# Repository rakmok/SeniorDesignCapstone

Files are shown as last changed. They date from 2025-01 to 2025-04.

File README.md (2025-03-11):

# SeniorDesignCapstone

This is the repository to record and motivate our capstone project for ECE 445: Senior Design in the Spring of 2025 titled PawFeast: Food on Demand. The group members are Arash Amiri, Kathryn Thompson, and Omkar Kulkarni.

The project entails the analysis, design, and build of a pet food dispensory system. If you wish to see each member's notebook, you can switch branches in github.com by clicking main or run git checkout \[member_first_name]-notebook. Each member hosts their own notebook on a different branch. The Hardware folder contains all of our KiCAD boards and other libraries. The images folder is only meant for displaying images to the README and the Assignments folder includes all of our important documents.

# Problem

All household pet owners must remember to feed their pets—whether they are birds, guinea pigs, rabbits, dogs, or cats—at set periods during the day. But there can be times when people forget to feed their pets, double feed them, or have trouble feeding them on schedule. This can be due to poor communication between family members or even occur when pet owners come home late from work or prior commitments. During these times, pets either overeat, go hungry, or eat irregularly. As a result, timer-based pet feeders have been developed to release food at set intervals. When food sits out for extended periods of time, the risk of the food becoming stale or getting infected with bugs increases drastically.

If an insect is near your food, it is a common reaction to remove or swat it away, but that mechanism is not present for the pet’s food bowl, especially when the family is not at home. Another issue is that smarter pets can nose into the food storage and overeat or eat something that their bodies will reject (like chocolate for dogs). With a set schedule to limit food dispensation throughout the day, the pet will not take advantage of either a careless overpour of food or of an unmanned food station. Furthermore, data on how much food was dispensed and eaten will help track and optimize the pet’s eating habits.

# Solution

We are seeking to solve this problem by having timers coupled with a button and RFID component to release food—thus preventing overeating. Given all of these conditions, the dispenser will release the pet food. This ensures that the pet is not only fed on time, but that the food is not polluted when the pet goes to eat; additionally, a chime will go off signaling to the pet that it is time for them to eat. We will incorporate a notification system to alert the owner(s) whether the pet has eaten or when the food store has low levels of food.

If the pet were to not eat all the food at once and leave the food dispenser, the pressure sensor will tell the dispenser to cover the food until the pet returns ensuring freshness and preventing bugs.

# Solution Components

## Subsystem 1: Refilling Food Store

The subsystem for checking if the food store is empty will include a through-beam optical sensor that is able to determine whether an object is present—this will serve to detect whether the food inside of the container is low and needs to be refilled. When the food store reaches a certain level, a signal will be sent to subsystem 6 (the brain), which will send an automated message to notify the owner to refill the food store.

## Subsystem 2: Power System

The power system will supply energy to all of the various subsystems, including the microcontroller of subsystem 6 (the brain), the stepper motor driver in subsystem 3, and the various sensors in subsystems 1 (refilling food) and 3 (food dispenser). The low voltage buses will be 3.3V, 12V, and 5V, all of which will be powered by a combination of rechargeable lithium-ion batteries with voltage regulators and buck converters. This compact, custom 3s2p battery pack will allow the pet dispenser to be portable, even for family vacations or road trips—more importantly, it will provide a steady current, even when the pack voltage drops (unlike standard AA/AAA cells). The 12V to 3.3V regulator chip will be Monolithic Power Systems’s MP2315SGJ-Z, which can take a 12V input and output up to 2.5A [4.7]. The 12V to 5V regulator chip will be Monolithic Power Systems’s MP2338GTL-Z [4.6]. The 12V input into the motor driver IC circuit will come straight from the battery pack. There will also be a backup supply voltage of 5V from a typical barrel jack wall-outlet, integrated into the brain board. This will implement the AMS1117 LDO, which is perfect for 5V to 3.3V power conversion. Just to be clear, this 5V barrel-jack addition will just be included on the brain board as a backup power subcircuit in case of power shutdown.

## Subsystem 3: Food Dispenser

This subsystem will utilize a E Series Nema 17 stepper motor that will rotate a door to the food container when needed and allow a set amount of food through before rotating again to close the door [4.8]. The motor will be controlled by a stepper motor controller IC (DRV8825) with a custom control circuit that takes in 12V and outputs 3.4V to the motor. We will define hard cut offs that will be coded for maximum amount of food to be dispensed and specify times at which food may be dispensed during the day.

The main objective of this subsystem is to make the system an on-demand food system. We will utilize a large button for the dog to step on when hungry. When pressed, the system will start the motors to release food, on the condition that enough time has elapsed since it ate last. The pet would be trained how to ask for food using this button. Only when the button is pressed and enough time has passed, will food then be dispensed.

## Subsystem 4: RFID for pet identification

We will have a receiver for a minimum of 2 HF RFID tags 9662 Long Distance Passive Alien H3. We will use the RC522 RFID chip for reading and writing to the RFID chips. The RFIDs would be used to signal which pet is using the dispenser, so the owner is able to utilize the same dispenser for one or more pets.

## Subsystem 5: User Interface

The subsystem for notifications will be a web application that we will build that is able to connect with the pet feed dispenser system. For the application side, we will utilize Bottle for our backend, SQLite for our database, and html pages for our frontend to create a user friendly method to check the pet’s eating habits. This will notify users for when the pet has been fed, if the food tank is low and requires refiling, and if the food was covered due to an empty bowl or a partially filled one.

## Subsystem 6: Brain

The brain subsystem will take in inputs from all of the other sensor subsystems and output the according signals to the user interface (for notifications) and the food dispenser motor driver. This system will also track the amount of time that has passed and sound a soft chime for when enough time has passed for the pet to be able to eat. The ESP32 WROOM-32E-4N microcontroller, known for its wifi connectivity and security measures, would have a set of I/O pins for taking in these signals. This MCU programmer circuit and other control level circuitry—firmware or equivalent—would be incorporated onto this board along with a UART circuit to detect pet RFIDs (done with the UHF RFID reader JRD-4035).

# High Level Requirements List

For this project to be considered successful, our project must meet the following requirements:

- The **Pet Food Dispenser** must **not** dispense food before user preset times, such as **10 AM and 6 PM, daily**, with a **10-minute tolerance**.
- The **Pet Food Dispenser** must dispense food into the **designated food bowl** upon detecting the **presence of the pet** via the **button** and the **2+ RFID tags** on the pet’s collar **within 2 minutes**.
- The **user interface** must update **within 5 minutes** of an event on the application we create, detailing:
  - The pet’s **feeding status**
  - **Low food store** notifications at **20% & 10%**
  - **Unfinished meals**

# Results

TBA

# Schematic

TBA

# Figures

TBA

# Demo

TBA

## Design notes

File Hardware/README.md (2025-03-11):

# KiCAD Board Repository

This is the hardware repository with all of our KiCAD boards. We have five: two power boards, a brain board, an RFID board, and the motor driver board. If you are unable to see symbols on the schematic capture, you will need to go to schematic editor->Preferences->Configure Paths and manually add a large parts library that you can link from Hardware/Libraries folder courtesey of Illini Solar Car.

For all of the parts that we dowloaded from 3rd party sites, there is a folder called Parts (Hardware/Parts), which has the symbols, footprints, and some .step files. This can be linked by going to schematic editor->Preferences->Manage Symbol Libraries. The same must be done for all the footprints in the PCB editor under Preferences->Manage Footprint Libraries. Three images below depict the path libraries for Omkar's KiCAD. Note that Omkar's file path for the Solar Car library is completely different and the Parts library is about three steps upstream from what you should link—you should add SeniorDesignCapstone/Hardware/Parts as your filepath instead of ../ECE445/Parts. There is also a courtesey template to get started, though you will need to set up the Illini Solar Car Libraries folder or you won't be able to retrieve parts with the 'a' hotkey.

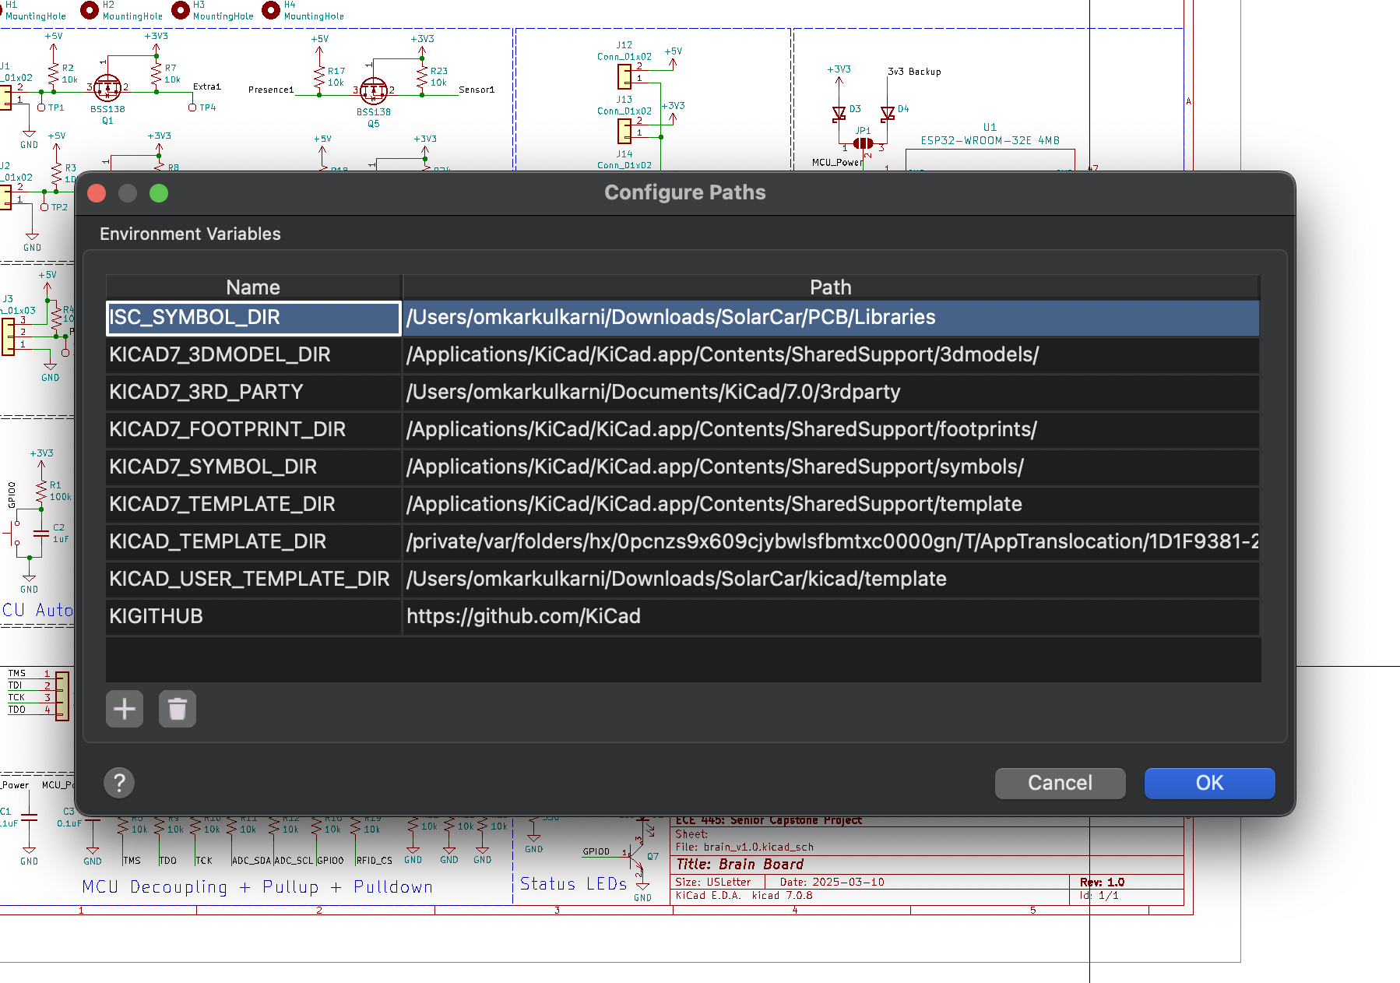
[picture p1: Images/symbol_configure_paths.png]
Configure Path

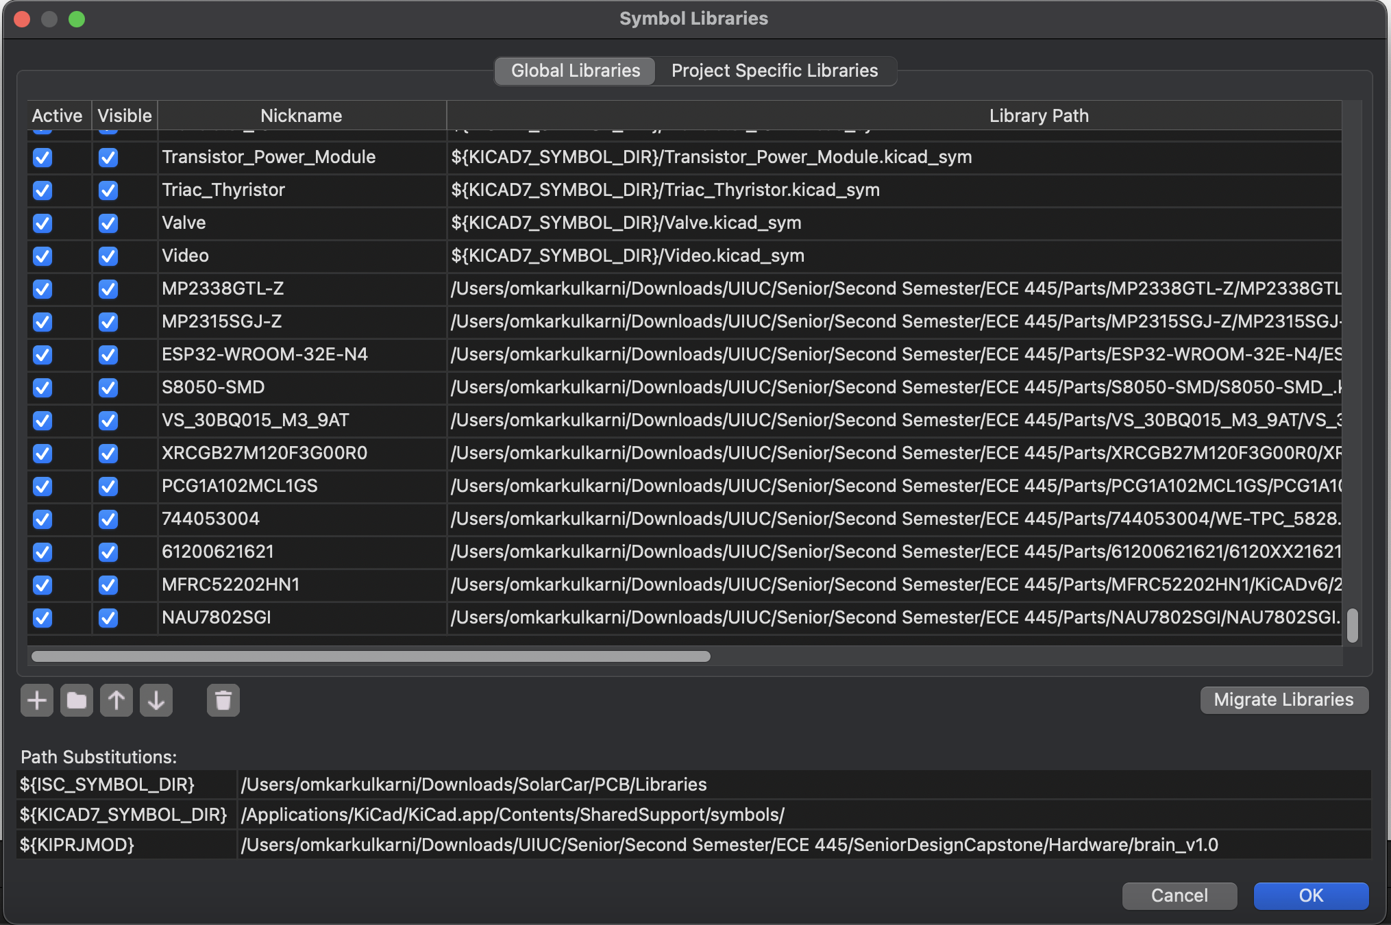
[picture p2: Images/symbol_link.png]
Download and Link Symbols

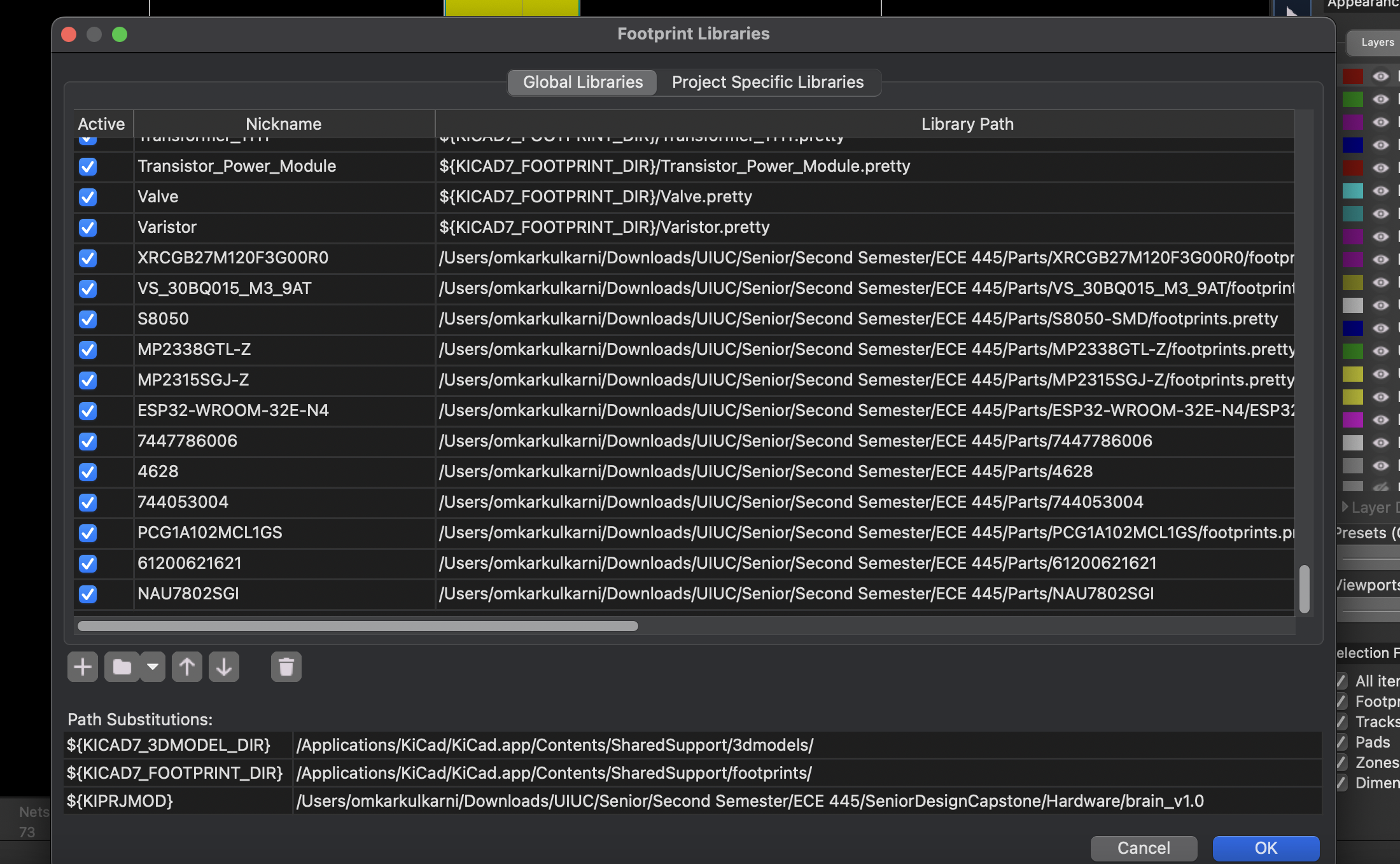
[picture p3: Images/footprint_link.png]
Download and Link Footprints


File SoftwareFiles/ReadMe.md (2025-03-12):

# Software Files for Team 30's Group Project for ECE445 at UIUC

This Markdown file will be used to describe the different files in this folder and what they do. Files that start with Arduino are comptible and tested on the Arduino UNO dev board for the breadboard demo. This code has been developed based on the provided starter code available on the distributer's website. We have included the links below for convenience.        

Works Cited:  
- [RFID](https://www.electronicwings.com/esp32/rfid-rc522-interfacing-with-esp32)
- [Load Cell (LC)](https://learn.adafruit.com/adafruit-nau7802-24-bit-adc-stemma-qt-qwiic/arduino) 
- [Presence Sensor (PS)](https://learn.adafruit.com/ir-breakbeam-sensors/arduino) 

The current organization of this folder is as follows:  
  [SoftwareFiles](./)  
  |-> [Arduino_RFID.cpp](./Arduino_RFID.cpp)  
  |-> [Arduino_LC.cpp](./Arduino_LC.cpp)  
  |-> [Arduino_PS.cpp](./Arduino_PS.cpp)  
  |-> [Arduino_RFID_LC_PS.cpp](./Arduino_RFID_LC_PS.cpp)

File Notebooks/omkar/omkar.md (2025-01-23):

# Omkar's Digital Notebook

This file serves as a digital notebook for my ECE 445: Senior Design project.

# 01/21/2025

After the first ECE 445 lecture, the group assembled to discuss and hash-out viable ideas for our project. We had previously met during winter break and gone through a number of project ideas related to solar power, cybersecurity, microcontroller development, vehicle architecure, cell balancing, and smart charging. In this session, the group researched ideas that fit the complexity and scope of what we believed was expected of us by the course staff. We made an initial project proposal post on the web board on smart charging technology, which includes battery health monitoring, voltage/current control, possibly the abilility to set charging percentage, and the ability to charge laptop-to-laptop. In this process, we discarded ideas related to cell-balancing and security because they were either too complex to implement or the group (as a whole) did not have enough expertise to pursue the idea.

We got an opportunity to ask the head TA about course logistics and project complexity. His feedback suggested that laptop-to-phone charging was too simple and if we wanted to work on high-voltage charging, every member of the group would need to get trained. Currently, we are assessing what is possible to complete within a semester and still complex enough to aim for being a featured project.

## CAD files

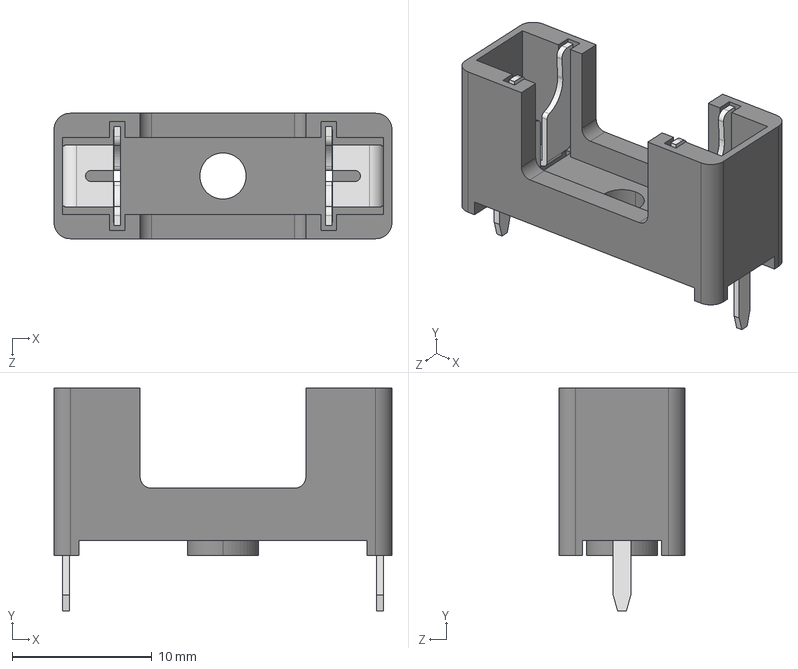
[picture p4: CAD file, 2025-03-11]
Hardware/Parts/4628/4628.step
24.2 x 16.0 x 8.99 mm

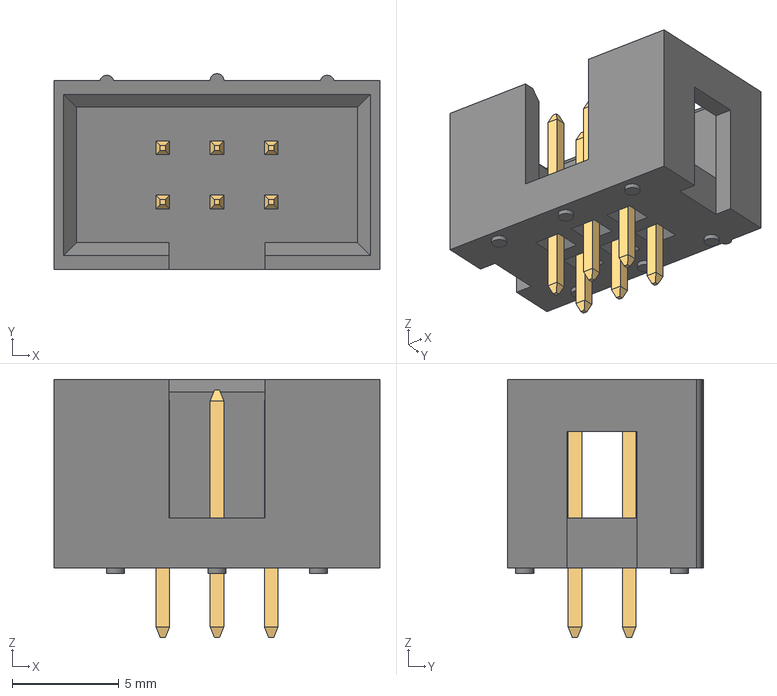
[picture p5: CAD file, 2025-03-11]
Hardware/Parts/61200621621/6120XX21621_61200621621.step
15.3 x 9.18 x 12.1 mm
6120xx21621_PIN x 6

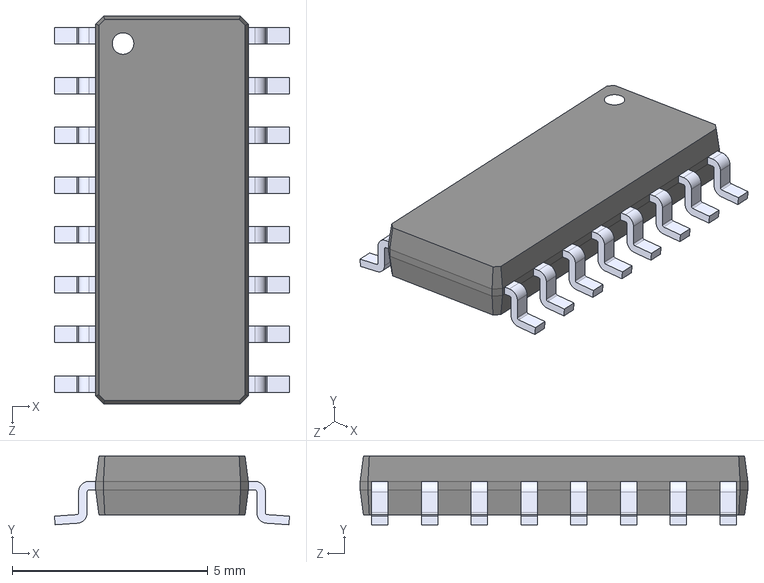
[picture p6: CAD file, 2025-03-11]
Hardware/Parts/NAU7802SGI/NAU7802SGI.step
6.00 x 1.75 x 9.90 mm

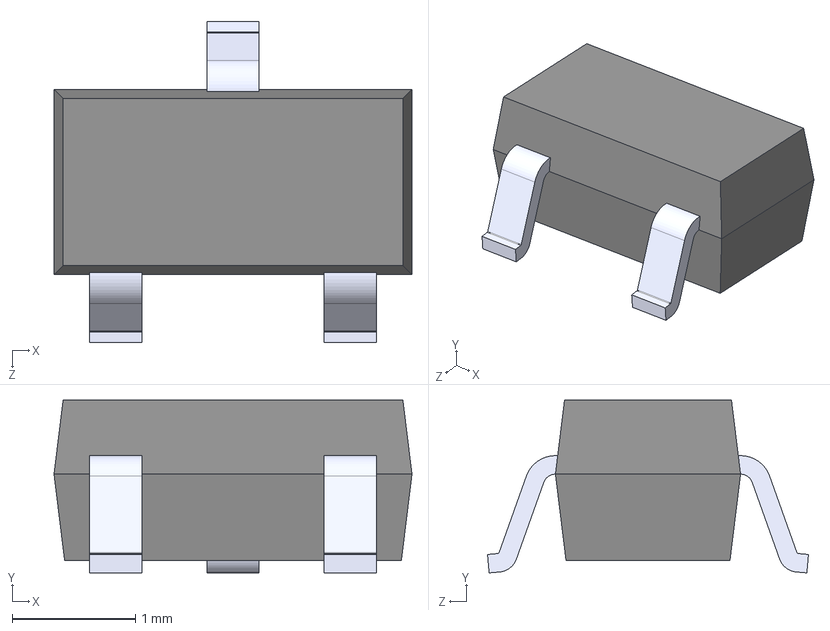
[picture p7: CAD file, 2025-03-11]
Hardware/Parts/S8050-SMD/S8050-SMD.step
2.90 x 1.40 x 2.60 mm

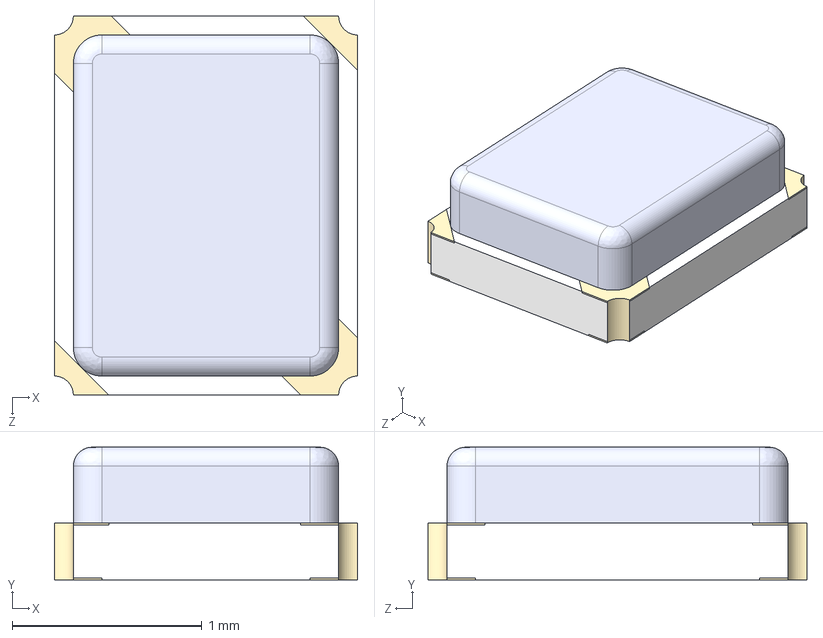
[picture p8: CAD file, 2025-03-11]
Hardware/Parts/XRCGB27M120F3G00R0/XRCGB27M120F3G00R0.step
1.60 x 0.7 x 2.00 mm

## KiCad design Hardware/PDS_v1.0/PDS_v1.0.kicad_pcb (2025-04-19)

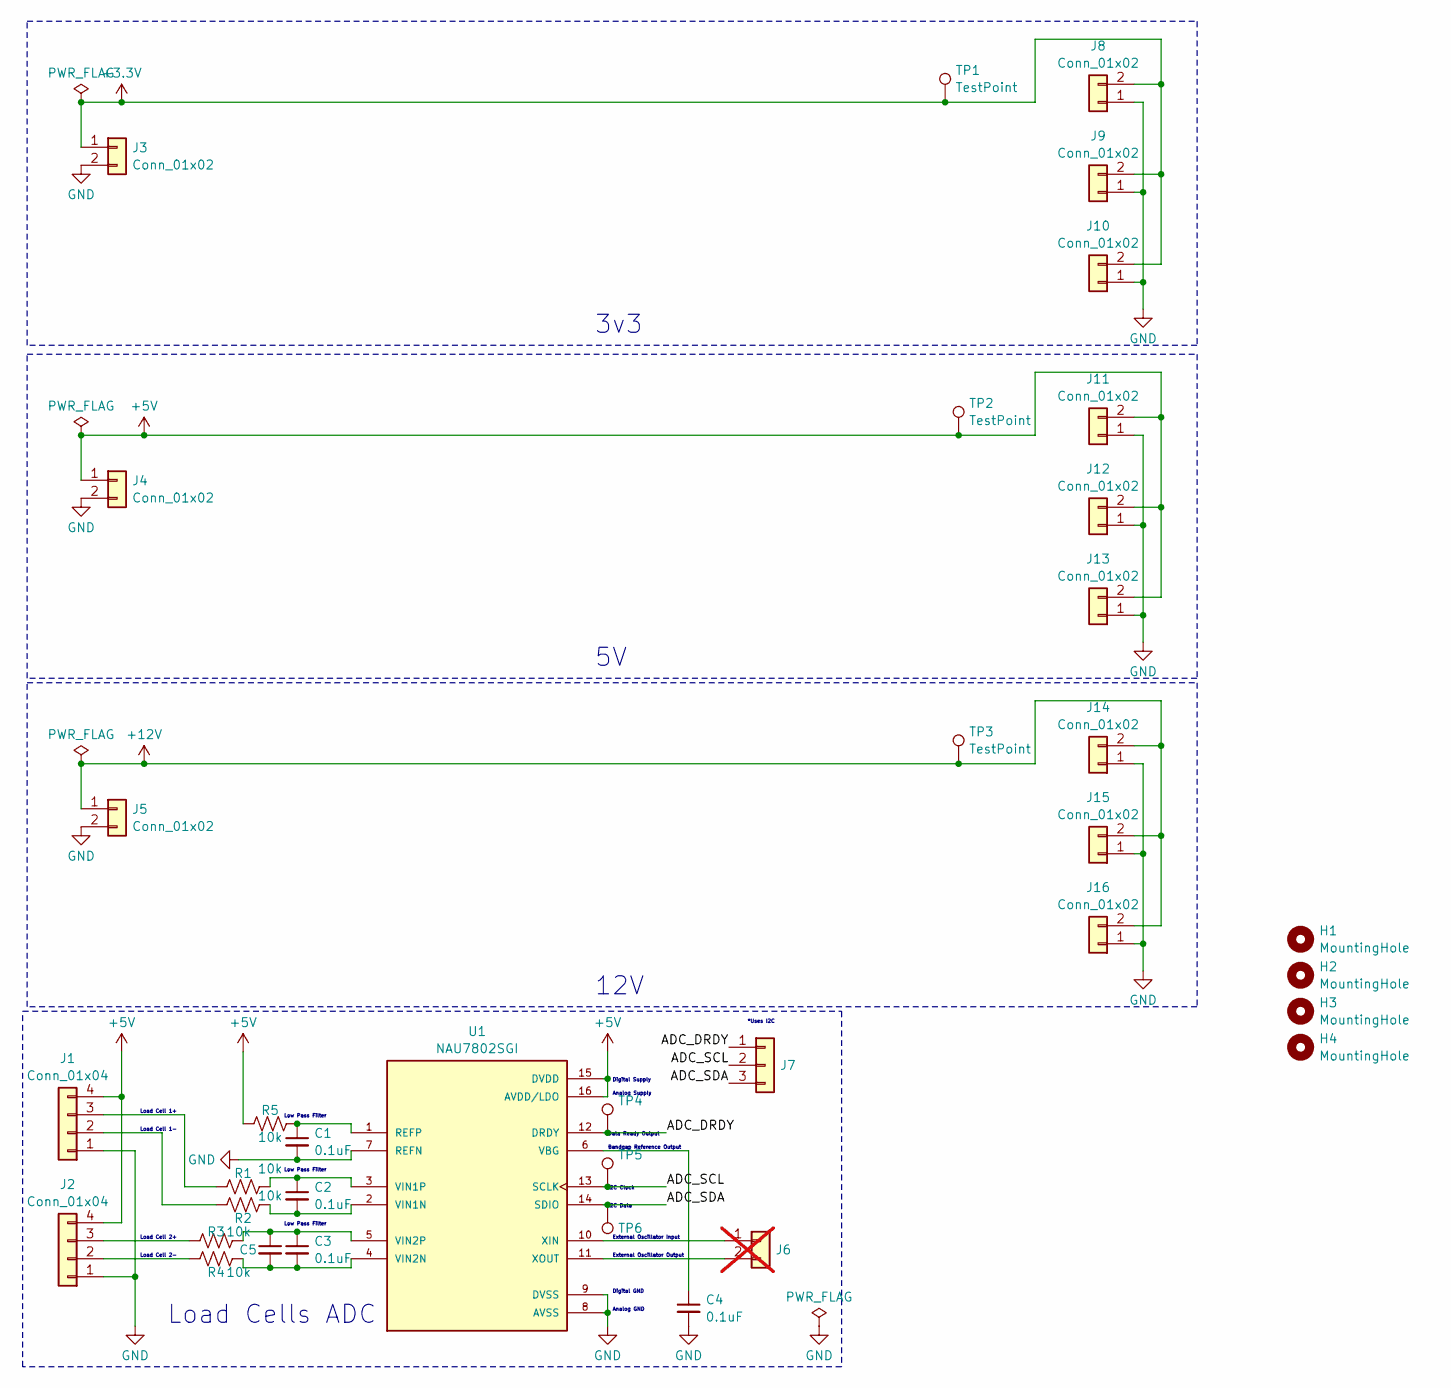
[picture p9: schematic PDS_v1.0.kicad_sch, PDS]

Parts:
C1, C2, C3, C4: 0.1uF; C_0805_2012Metric; MPN CC0603KRX7R7BB104
C5: 470uF; C_Radial_D10.0mm_H12.5mm_P5.00mm
H1, H2, H3, H4: MountingHole; MountingHole_3.2mm_M3; MPN NA
J1, J2: Conn_01x04; Molex_KK-254_AE-6410-04A_1x04_P2.54mm_Vertical; MPN 0022292041
J3, J4, J5, J8, J9, J10, J11, J12, J13, J14, J15, J16: Conn_01x02; Molex_KK-254_AE-6410-02A_1x02_P2.54mm_Vertical
J6: Conn_01x02; Molex_KK-254_AE-6410-02A_1x02_P2.54mm_Vertical; not fitted
J7: Conn_01x03; Molex_KK-254_AE-6410-03A_1x03_P2.54mm_Vertical
R1, R2, R3, R4, R5: 10k; R_0805_2012Metric; MPN HRG3216P-1002-B-T1
TP1, TP2, TP3, TP4, TP5, TP6: TestPoint; TestPoint_Keystone_5010-5014_Multipurpose
U1: NAU7802SGI; SOIC127P600X175-16N; PARTREV 2.6

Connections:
+3V3: J3.1, J8.2, J9.2, J10.2, TP1.1
+5V: J1.4, J2.4, J4.1, J11.2, J12.2, J13.2, R5.1, TP2.1, U1.15 (DVDD), U1.16 (AVDD/LDO)
+12V: J5.1, J14.2, J15.2, J16.2, TP3.1
/ADC_DRDY: J7.1, TP4.1, U1.12 (DRDY)
/ADC_SCL: J7.2, TP5.1, U1.13 (SCLK)
/ADC_SDA: J7.3, TP6.1, U1.14 (SDIO)
GND: C1.2, C4.2, J1.1, J2.1, J3.2, J4.2, J5.2, J8.1, J9.1, J10.1, J11.1, J12.1, J13.1, J14.1, J15.1, J16.1, U1.7 (REFN), U1.8 (AVSS), U1.9 (DVSS)
unnamed: J1.2, R2.1
unnamed: J1.3, R1.1
unnamed: J2.2, R4.1
unnamed: J2.3, R3.1
unnamed: J6.1, U1.10 (XIN)
unnamed: J6.2, U1.11 (XOUT)
unnamed: C1.1, R5.2, U1.1 (REFP)
unnamed: C4.1, U1.6 (VBG)
unnamed: C2.2, R2.2, U1.2 (VIN1N)
unnamed: C2.1, R1.2, U1.3 (VIN1P)
unnamed: C3.2, C5.2, R4.2, U1.4 (VIN2N)
unnamed: C3.1, C5.1, R3.2, U1.5 (VIN2P)

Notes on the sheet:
Load Cell 2-
Low Pass Filter
Analog GND
3v3
Load Cell 2+
Load Cell 1+
12V
Analog Supply
Digital Supply
*Uses I2C
Load Cells ADC
Bandgap Reference Output
External Oscillator Input
Data Ready Output
Digital GND
I2C Data
External Oscillator Output
Load Cell 1-
I2C Clock

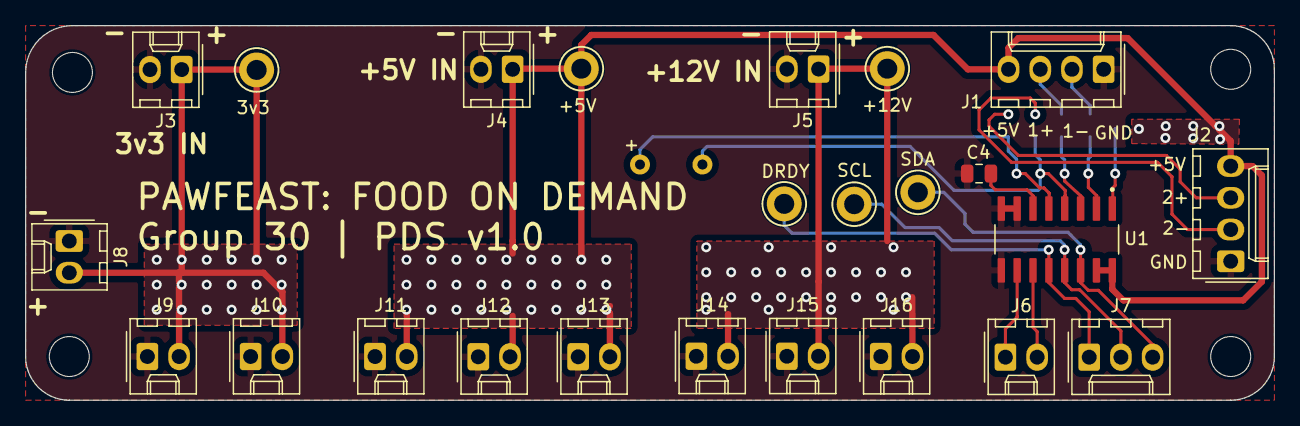
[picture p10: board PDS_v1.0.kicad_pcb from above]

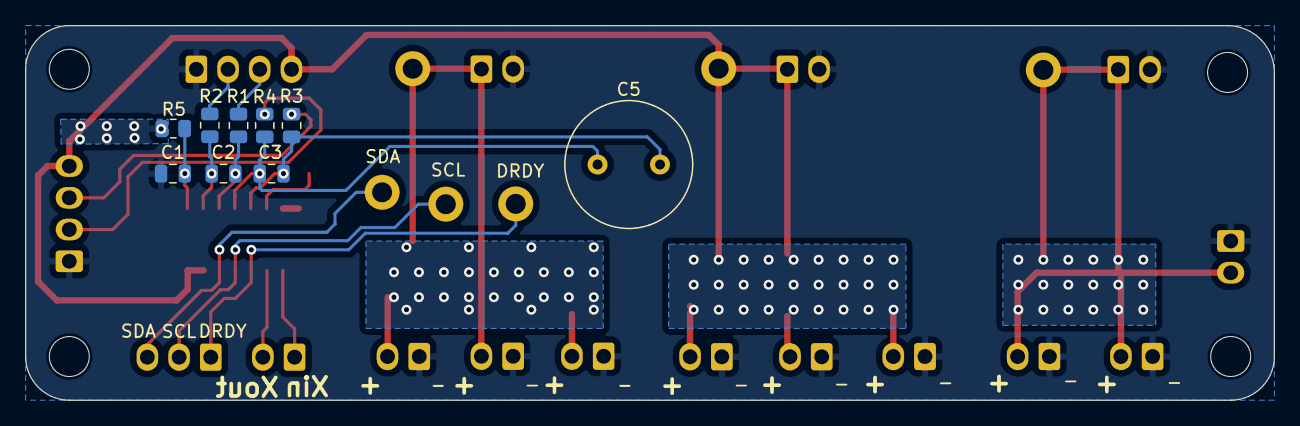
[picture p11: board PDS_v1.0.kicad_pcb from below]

Board: 2 copper layers, 100.0 x 30.0 mm, 37 parts (9 on the bottom side), 19 nets.

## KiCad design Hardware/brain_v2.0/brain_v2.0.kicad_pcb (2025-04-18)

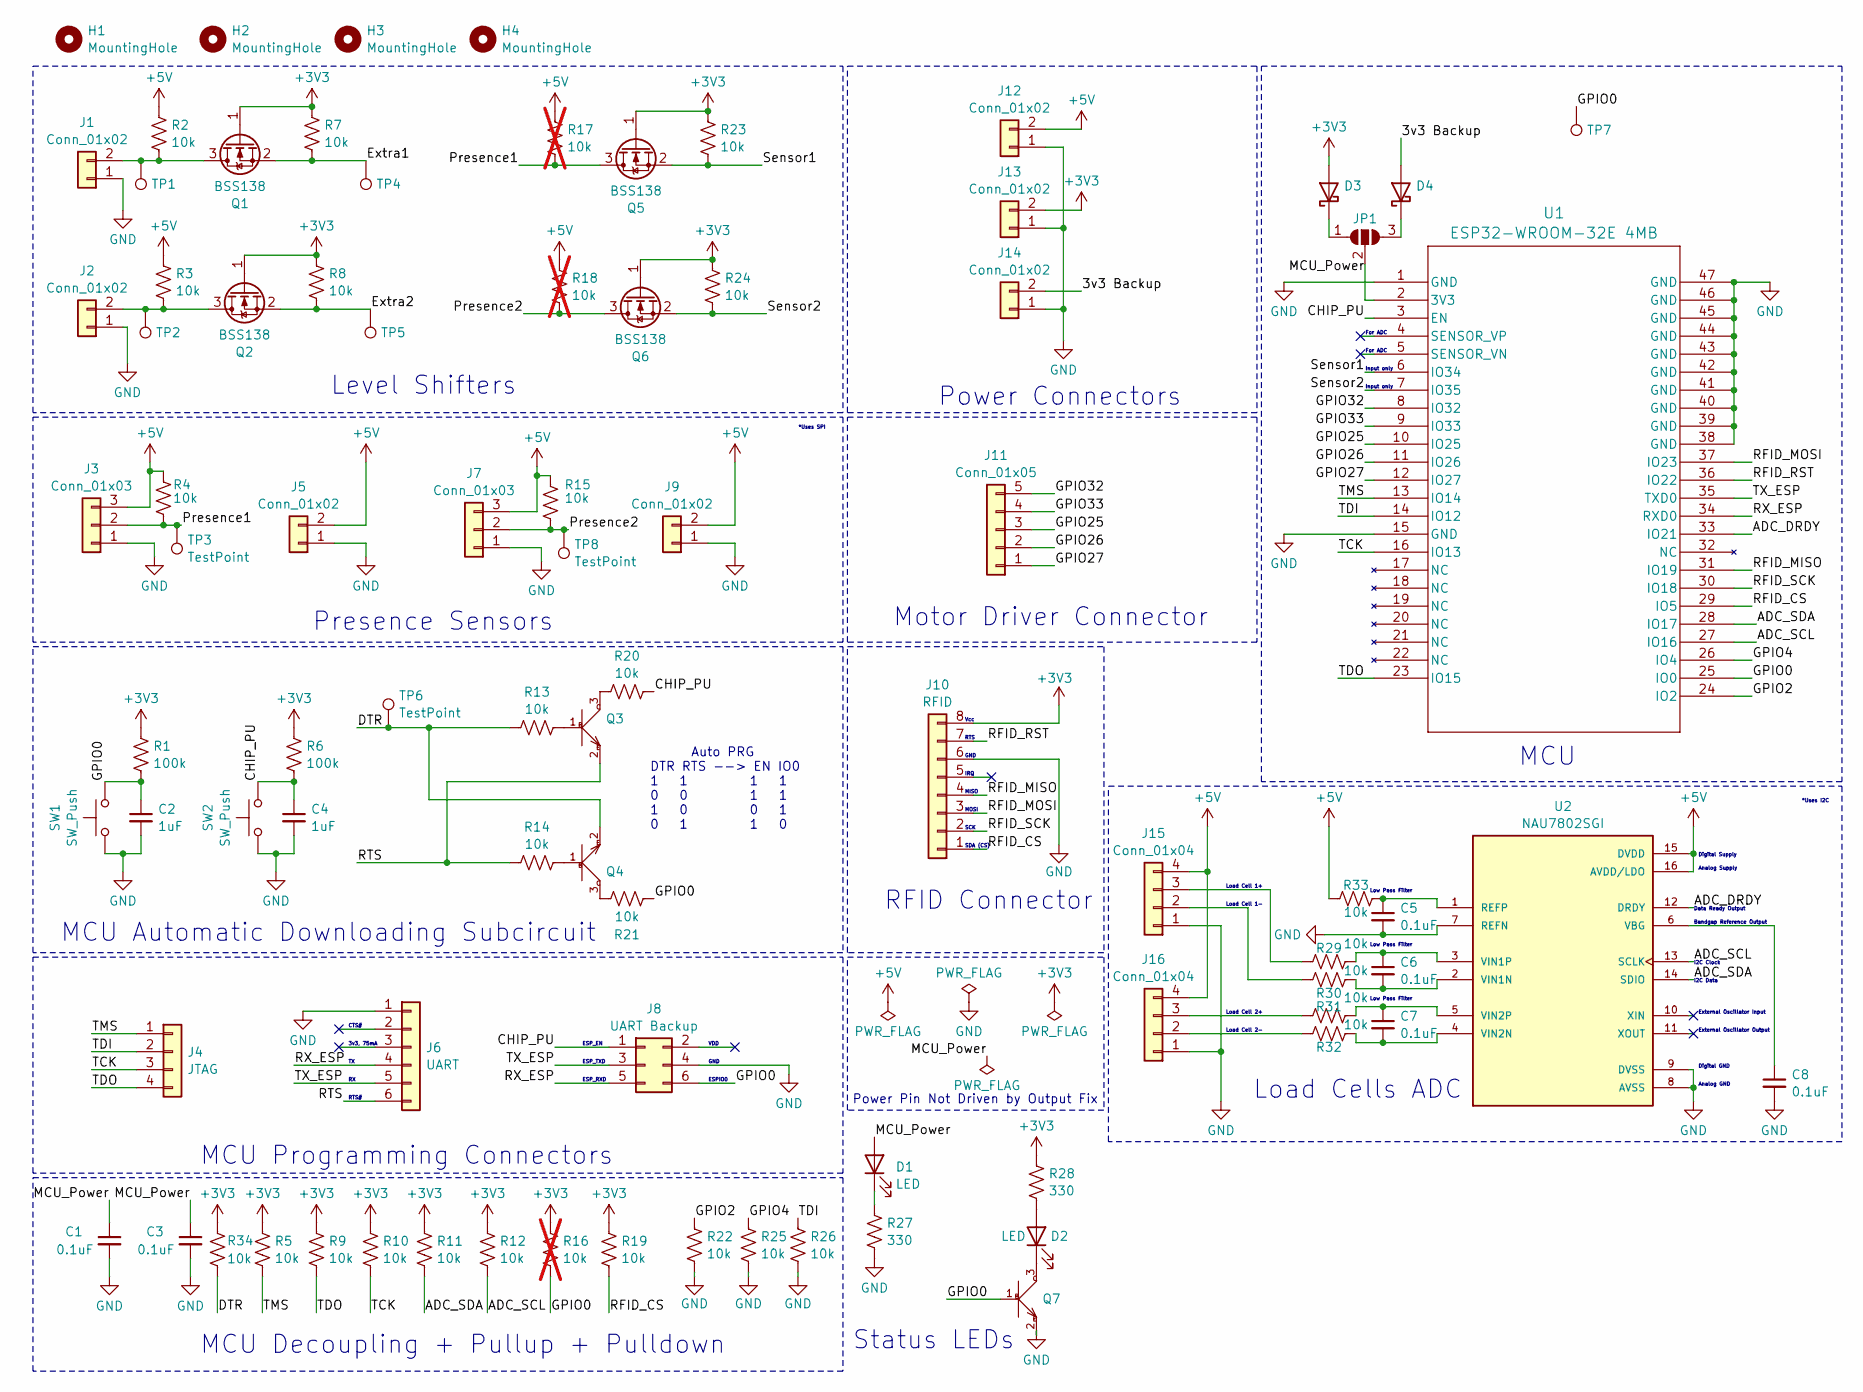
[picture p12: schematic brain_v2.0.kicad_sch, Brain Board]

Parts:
C1, C3: 0.1uF; C_0603_1608Metric; MPN C0603C103F3GECAUTO
C2, C4: 1uF; R_0603_1608Metric; MPN TMK107B7105KA-T
C5, C6, C7, C8: 0.1uF; C_0603_1608Metric; MPN CC0603KRX7R7BB104
D1: LED; LED_0603_1608Metric; MPN LTST-C191KFKT
D2: LED; LED_0603_1608Metric; MPN LTST-C190GKT
D3, D4: D_Schottky; VS_30BQ015_M3_9AT; MPN VS-30BQ015-M3/9AT
H1, H2, H3, H4: MountingHole; MountingHole_3.2mm_M3; MPN NA
J1, J2, J5, J9, J12, J13, J14: Conn_01x02; Molex_KK-254_AE-6410-02A_1x02_P2.54mm_Vertical; MPN 1718560102
J3, J7: Conn_01x03; Molex_KK-254_AE-6410-03A_1x03_P2.54mm_Vertical; MPN 0022272031
J4: JTAG; PinSocket_1x04_P2.54mm_Vertical; MPN M20-9990446
J6: UART; PinHeader_1x06_P2.54mm_Vertical; MPN M20-9990645
J8: UART Backup; 61200621621; MPN 61200621621
J10: RFID; Harting_har-flexicon_14110813001xxx_1x08-MP_P2.54mm_Vertical; MPN 14110813001000
J11: Conn_01x05; PinHeader_1x05_P2.54mm_Vertical; MPN M20-9990546
J15, J16: Conn_01x04; Molex_KK-254_AE-6410-04A_1x04_P2.54mm_Vertical; MPN 0022292041
JP1: SolderJumper_3_Open; SolderJumper-3_P1.3mm_Open_RoundedPad1.0x1.5mm; MPN NA
Q1, Q2, Q5, Q6: BSS138; SOT-23; MPN BSS138
Q3, Q4, Q7: SMD-TRANSISTORS-NPN-25V-500MW_SOT-23_; S8050-SMD; MPN S8050; DigiKey_Part_Number 3372-S8050TR-ND
R1, R6: 100k; R_0805_2012Metric; MPN RC0805FR-07100KL
R2, R3, R4, R5, R7, R8, R9, R10, R11, R12, R13, R14, R15, R19, R20, R21, R22, R23, R24, R25, R26, R29, R30, R31, R32, R33, R34: 10k; R_1206_3216Metric; MPN HRG3216P-1002-B-T1
R16, R17, R18: 10k; R_1206_3216Metric; MPN HRG3216P-1002-B-T1; not fitted
R27, R28: 330; R_0603_1608Metric
SW1, SW2: SW_Push; SW_SPST_B3U-1000P; MPN B3U-1000P
TP1, TP2, TP3, TP4, TP5, TP6, TP7, TP8: TestPoint; TestPoint_Keystone_5010-5014_Multipurpose; MPN 36-5011-ND
U1: ESP32-WROOM-32E 4MB; ESP32-WROOM-32E-N4; MPN ESP32-WROOM-32E-N4
U2: NAU7802SGI; SOIC127P600X175-16N; PARTREV 2.6

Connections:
+3V3: D3.2 (A), J10.8, J13.2, Q1.1 (G), Q2.1 (G), Q5.1 (G), Q6.1 (G), R1.1, R5.1, R6.1, R7.1, R8.1, R9.1, R10.1, R11.1, R12.1, R16.1, R19.1, R23.1, R24.1, R28.1, R34.1
+5V: J3.3, J5.2, J7.3, J9.2, J12.2, J15.4, J16.4, R2.1, R3.1, R4.1, R15.1, R17.1, R18.1, R33.1, U2.15 (DVDD), U2.16 (AVDD/LDO)
/3v3 Backup: D4.2 (A), J14.2
/ADC_DRDY: U1.33 (IO21), U2.12 (DRDY)
/ADC_SCL: R12.2, U1.27 (IO16), U2.13 (SCLK)
/ADC_SDA: R11.2, U1.28 (IO17), U2.14 (SDIO)
/CHIP_PU: C4.1, J8.1, R6.2, R20.2, SW2.2, U1.3 (EN)
/DTR: Q4.2, R13.1, R34.2, TP6.1
/Extra1: Q1.2 (S), R7.2, TP4.1
/Extra2: Q2.2 (S), R8.2, TP5.1
/GPIO0: C2.1, J8.6, Q7.1, R1.2, R16.2, R21.2, SW1.2, TP7.1, U1.25 (IO0)
/GPIO2: R22.1, U1.24 (IO2)
/GPIO4: R25.1, U1.26 (IO4)
/GPIO25: J11.3, U1.10 (IO25)
/GPIO26: J11.2, U1.11 (IO26)
/GPIO27: J11.1, U1.12 (IO27)
/GPIO32: J11.5, U1.8 (IO32)
/GPIO33: J11.4, U1.9 (IO33)
/MCU_Power: C1.1, C3.1, D1.2 (A), JP1.2 (C), U1.2 (3V3)
/Presence1: J3.2, Q5.3 (D), R4.2, R17.2, TP3.1
/Presence2: J7.2, Q6.3 (D), R15.2, R18.2, TP8.1
/RFID_CS: J10.1, R19.2, U1.29 (IO5)
/RFID_MISO: J10.4, U1.31 (IO19)
/RFID_MOSI: J10.3, U1.37 (IO23)
/RFID_RST: J10.7, U1.36 (IO22)
/RFID_SCK: J10.2, U1.30 (IO18)
/RTS: J6.6, Q3.2, R14.1
/RX_ESP: J6.4, J8.5, U1.34 (RXD0)
/Sensor1: Q5.2 (S), R23.2, U1.6 (IO34)
/Sensor2: Q6.2 (S), R24.2, U1.7 (IO35)
/TCK: J4.3, R10.2, U1.16 (IO13)
/TDI: J4.2, R26.1, U1.14 (IO12)
/TDO: J4.4, R9.2, U1.23 (IO15)
/TMS: J4.1, R5.2, U1.13 (IO14)
/TX_ESP: J6.5, J8.3, U1.35 (TXD0)
GND: C1.2, C2.2, C3.2, C4.2, C5.2, C8.2, J1.1, J2.1, J3.1, J5.1, J6.1, J7.1, J8.4, J9.1, J10.6, J12.1, J13.1, J14.1, J15.1, J16.1, Q7.2, R22.2, R25.2, R26.2, R27.2, SW1.1, SW2.1, U1.1 (GND), U1.15 (GND), U1.38 (GND), U1.39 (GND), U1.40 (GND), U1.41 (GND), U1.42 (GND), U1.43 (GND), U1.44 (GND), U1.45 (GND), U1.46 (GND), U1.47 (GND), U2.7 (REFN), U2.8 (AVSS), U2.9 (DVSS)
unnamed: D1.1 (K), R27.1
unnamed: D2.2 (A), R28.2
unnamed: D2.1 (K), Q7.3
unnamed: D3.1 (K), JP1.1 (A)
unnamed: D4.1 (K), JP1.3 (B)
unnamed: J1.2, Q1.3 (D), R2.2, TP1.1
unnamed: J2.2, Q2.3 (D), R3.2, TP2.1
unnamed: J15.2, R30.1
unnamed: J15.3, R29.1
unnamed: J16.2, R32.1
unnamed: J16.3, R31.1
unnamed: Q3.1, R13.2
unnamed: Q3.3, R20.1
unnamed: Q4.1, R14.2
unnamed: Q4.3, R21.1
unnamed: C5.1, R33.2, U2.1 (REFP)
unnamed: C8.1, U2.6 (VBG)
unnamed: C6.2, R30.2, U2.2 (VIN1N)
unnamed: C6.1, R29.2, U2.3 (VIN1P)
unnamed: C7.2, R32.2, U2.4 (VIN2N)
unnamed: C7.1, R31.2, U2.5 (VIN2P)

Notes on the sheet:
Load Cell 1-
Low Pass Filter
Digital Supply
Load Cells ADC
Power Pin Not Driven by Output Fix
For ADC
RFID Connector
Load Cell 2-
ESPIO0
Auto PRG DTR RTS --> EN IO0 1 1 1 1 0 0 1 1 1 0 0 1 0 1 1 0
IRQ
ESP_TXD
I2C Data
MCU
Analog Supply
Digital GND
SCK
RTS
Load Cell 2+
CTS#
RTS#
VDD
Load Cell 1+
MCU Decoupling + Pullup + Pulldown
GND
MOSI
MCU Programming Connectors
MISO
External Oscillator Output
*Uses I2C
ESP_EN
MCU Automatic Downloading Subcircuit
Status LEDs
Input only
Power Connectors
Presence Sensors
Bandgap Reference Output
*Uses SPI
Level Shifters
Motor Driver Connector

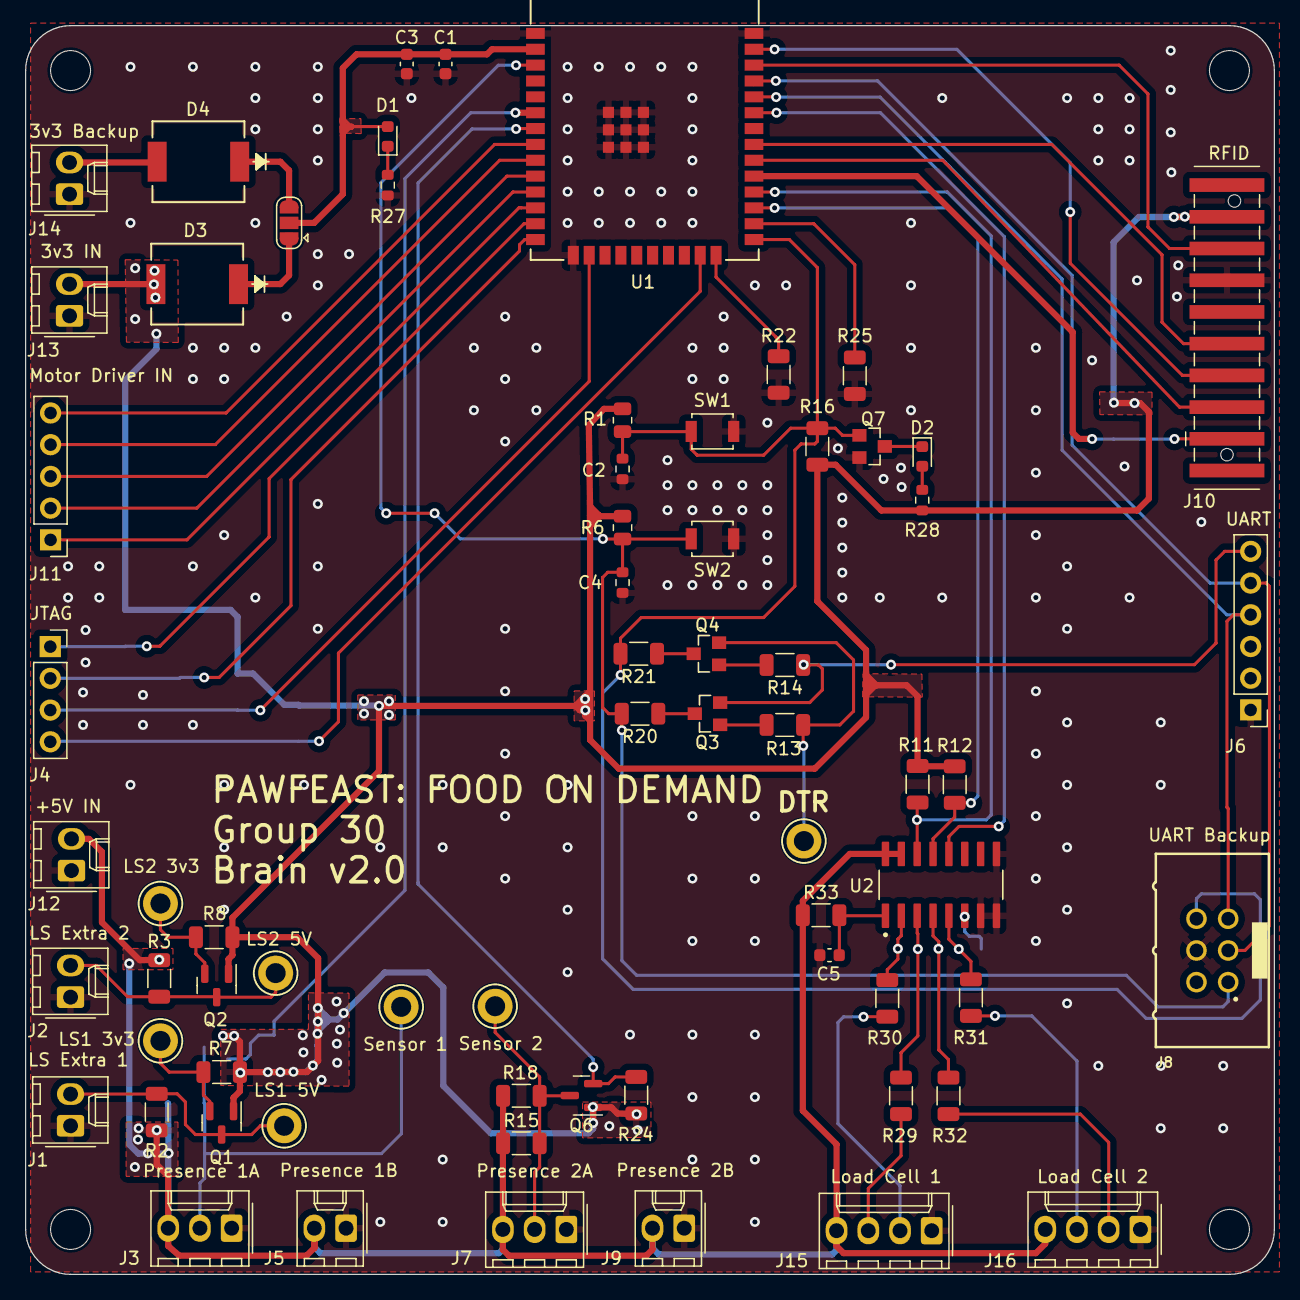
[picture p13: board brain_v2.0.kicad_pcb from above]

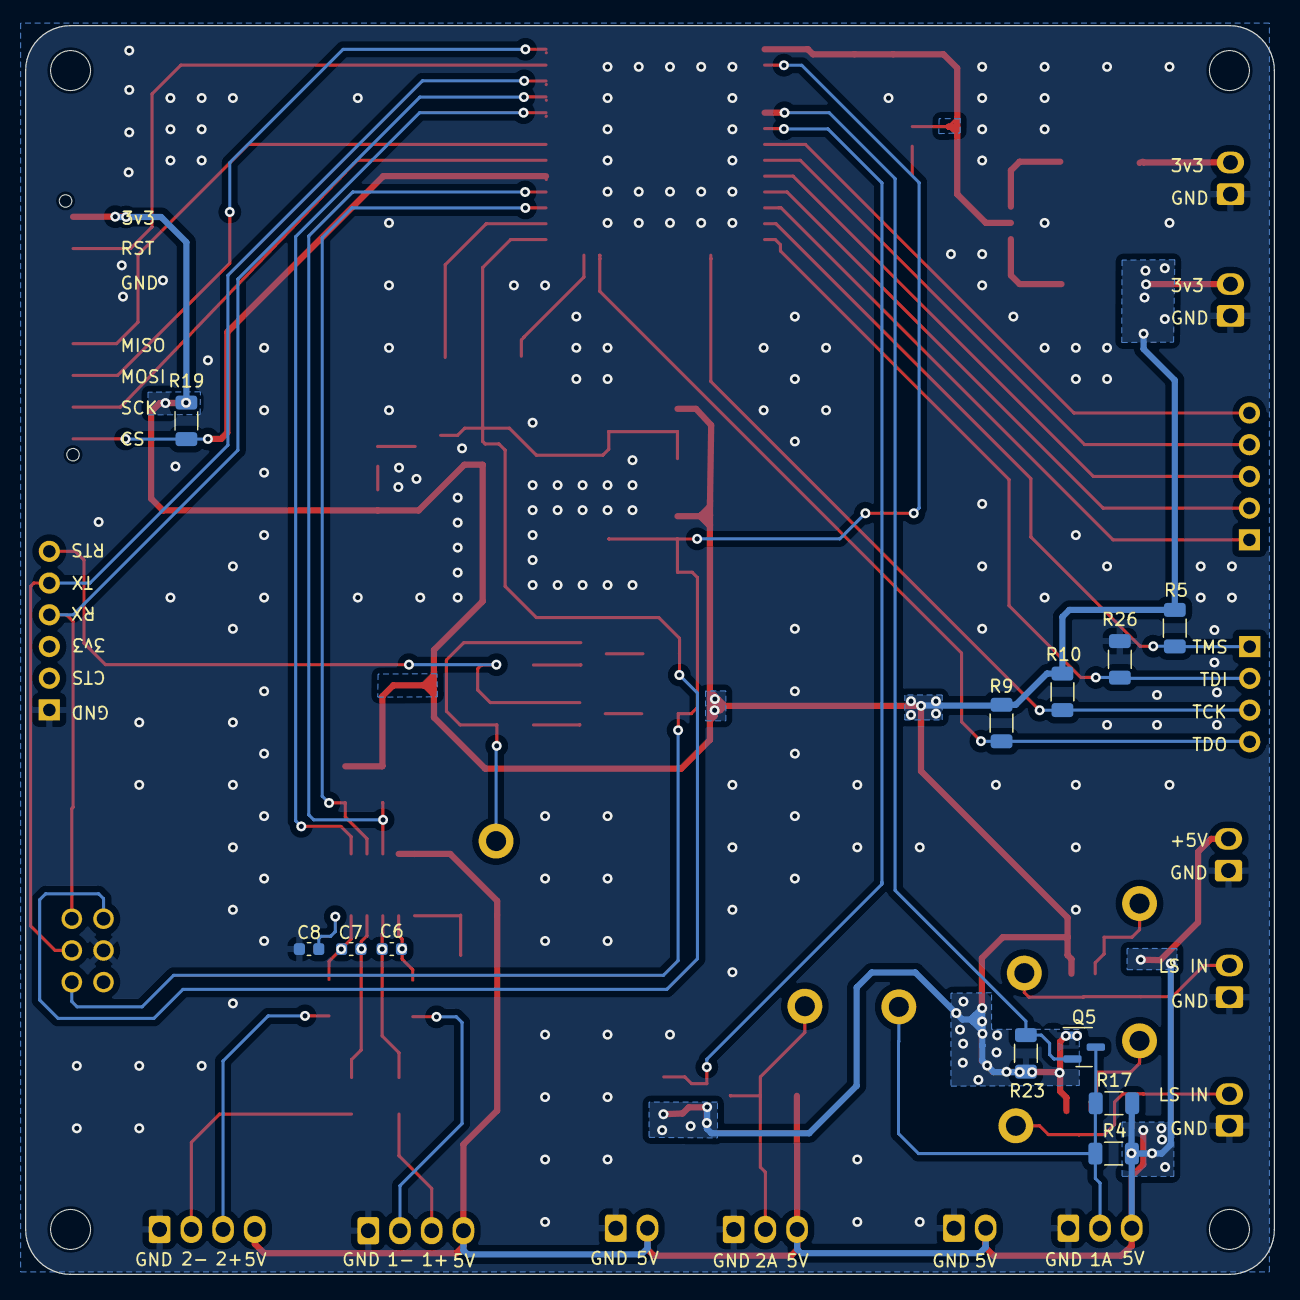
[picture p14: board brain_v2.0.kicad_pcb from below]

Board: 2 copper layers, 100.0 x 100.0 mm, 84 parts (12 on the bottom side), 57 nets.

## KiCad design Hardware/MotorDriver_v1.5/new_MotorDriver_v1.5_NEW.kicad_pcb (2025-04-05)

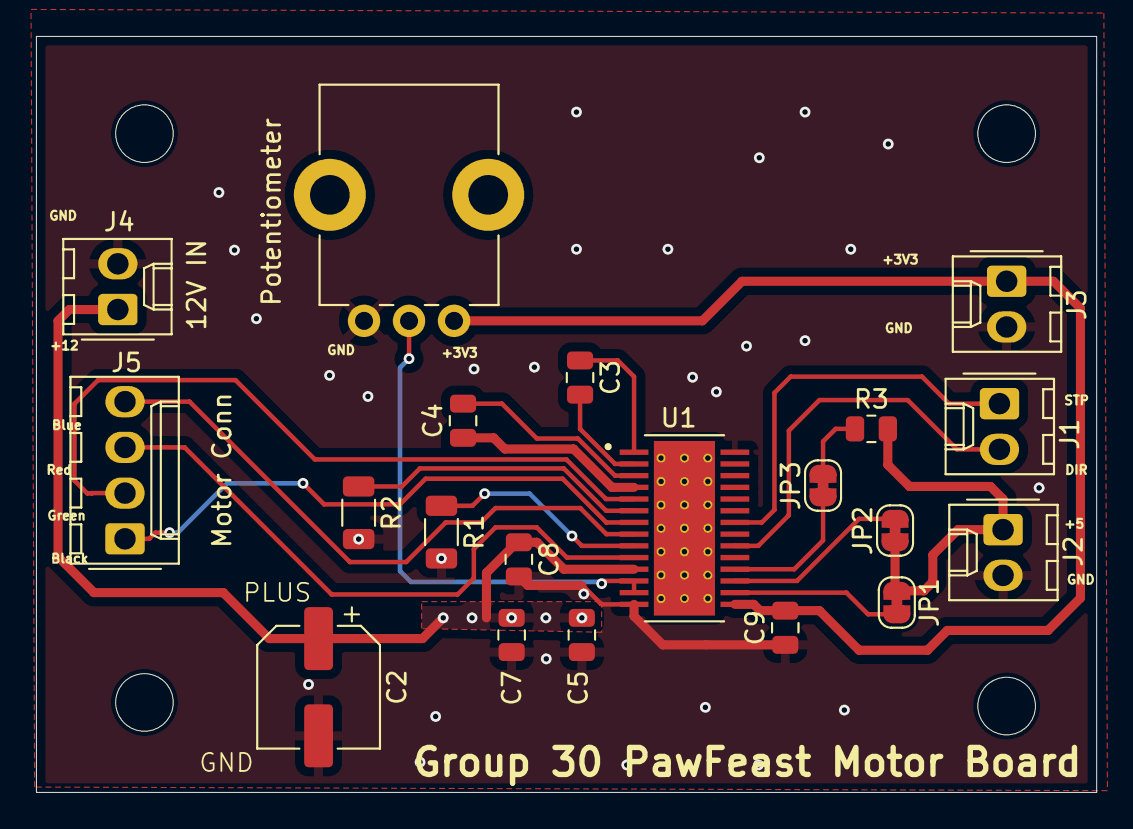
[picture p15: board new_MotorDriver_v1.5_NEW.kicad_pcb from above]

Board: 2 copper layers, 58.9 x 42.0 mm, 24 parts (0 on the bottom side), 20 nets.

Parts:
12V IN: 12V Pwr; Molex_KK-254_AE-6410-02A_1x02_P2.54mm_Vertical
C2: 100uF; CP_Elec_6.3x5.8
C3: 10uF; C_0805_2012Metric
C4, C7, C8: 0.1uF; C_0805_2012Metric
C5: 4.7uF; C_0805_2012Metric
C9: 0.47uF; C_0805_2012Metric
H1, H2, H3, H4: MountingHole; MountingHole_3.2mm_M3
J1, J2, J3: Conn_01x02; Molex_KK-254_AE-6410-02A_1x02_P2.54mm_Vertical
JP1, JP2, JP3: SolderJumper_2_Bridged; SolderJumper-2_P1.3mm_Bridged_RoundedPad1.0x1.5mm
Motor Conn: J5; Molex_KK-254_AE-6410-04A_1x04_P2.54mm_Vertical
Potentiometer: 10k; Potentiometer_Bourns_PTV09A-1_Single_Vertical
R1, R2: 0.10; R_1206_3216Metric
R3: 10k; R_0805_2012Metric
U1: DRV8825PWPR; IC_TPS61196PWPRQ1

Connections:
+3V3: C9.2, J3.1, Potentiometer.1, U1.15 (V3P3OUT)
+5V: J2.1, JP1.1 (A), JP2.1 (A), R3.2
+12V: 12V IN.1, C2.1, C4.1, C5.1, C7.1, C8.1, U1.4 (VMA), U1.11 (VMB)
/DIR: J1.2, U1.20 (DIR)
/STP: J1.1, U1.22 (STEP)
GND: 12V IN.2, C2.2, C5.2, C7.2, C8.2, C9.1, J2.2, J3.2, Potentiometer.3, R1.2, R2.2, U1.14 (GND), U1.28 (GND)
unnamed: Motor Conn.1, U1.7 (AOUT2)
unnamed: Motor Conn.2, U1.5 (AOUT1)
unnamed: Motor Conn.3, U1.10 (BOUT1)
unnamed: Motor Conn.4, U1.8 (BOUT2)
unnamed: JP1.2 (B), U1.16 (~NRESET)
unnamed: JP2.2 (B), U1.17 (NSLEEP)
unnamed: JP3.1 (A), U1.18 (NFAULT)
unnamed: JP3.2 (B), R3.1
unnamed: Potentiometer.2, U1.12 (AVREF), U1.13 (BVREF)
unnamed: C3.1, U1.1 (CP1)
unnamed: C3.2, U1.2 (CP2)
unnamed: R2.1, U1.6 (ISENA)
unnamed: R1.1, U1.9 (ISENB)
unnamed: C4.2, U1.3 (VCP)

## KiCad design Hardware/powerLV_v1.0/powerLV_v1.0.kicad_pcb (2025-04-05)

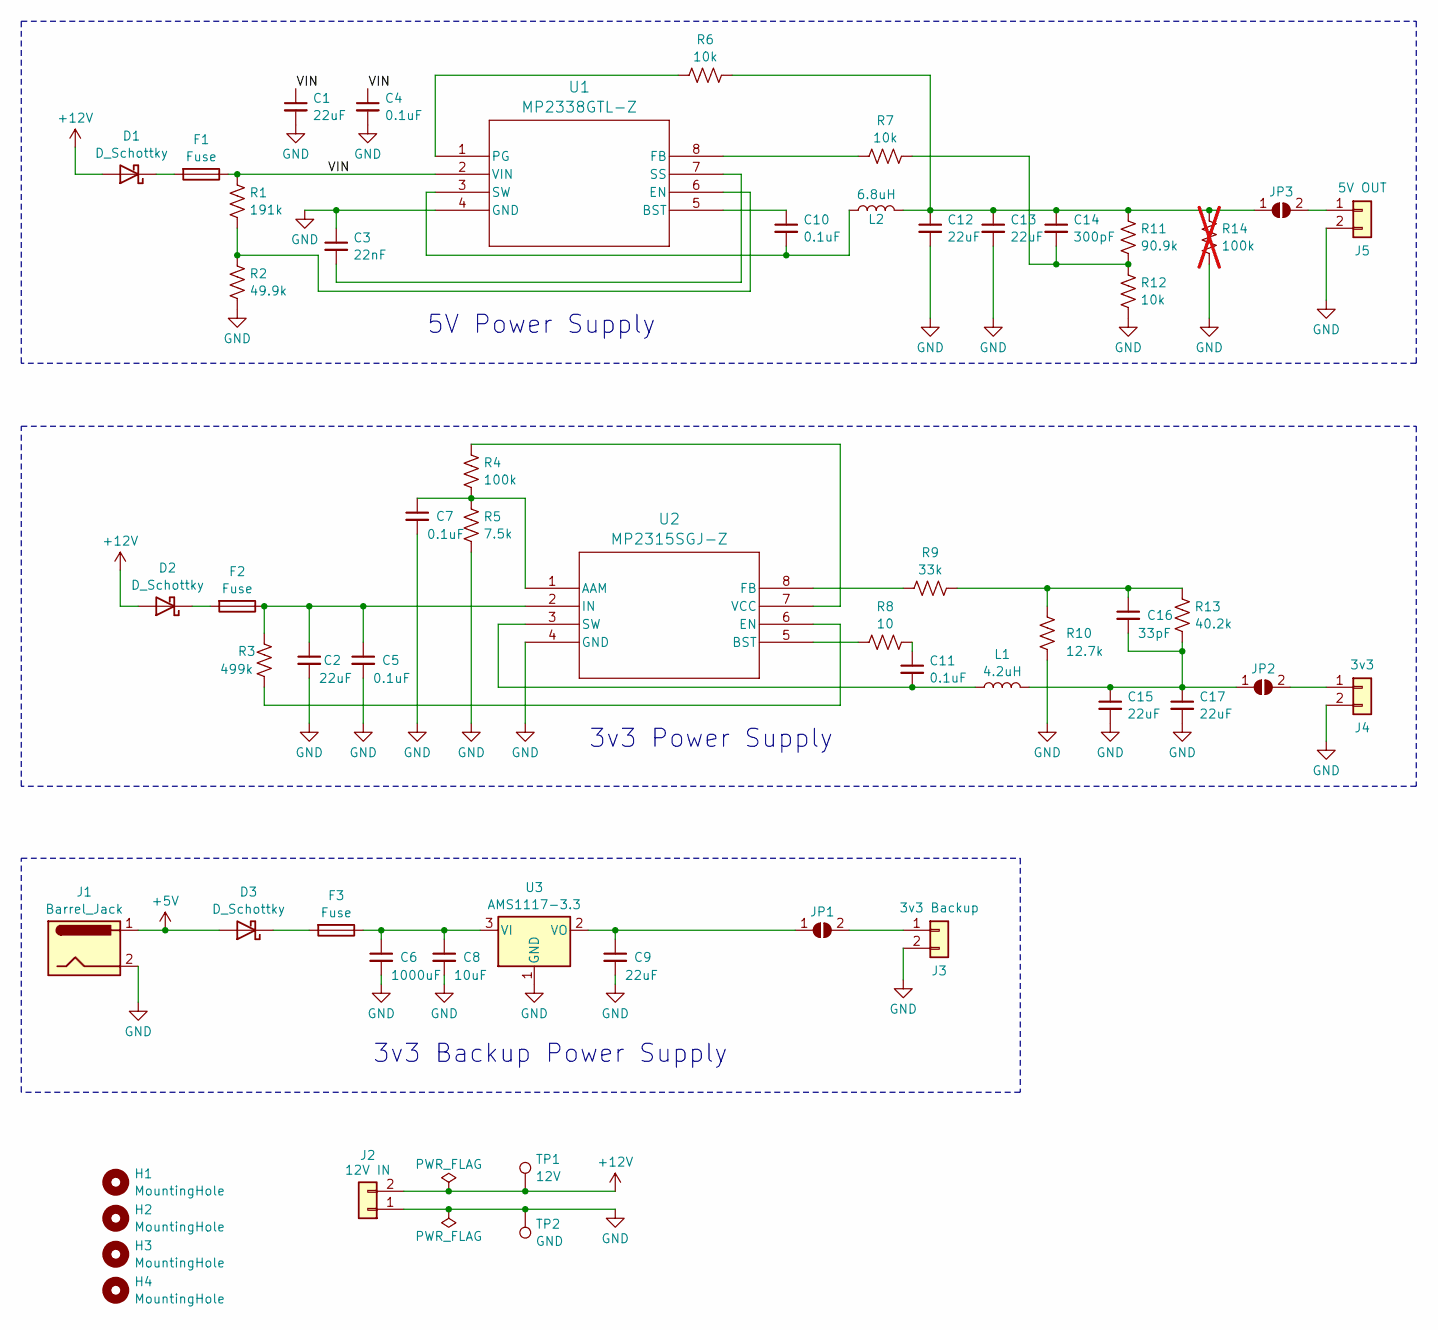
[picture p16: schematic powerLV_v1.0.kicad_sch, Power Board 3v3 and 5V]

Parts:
C1, C2, C9, C12, C13, C15, C17: 22uF; C_0805_2012Metric; MPN CL21A226MAYNNNE
C3: 22nF; C_0805_2012Metric; MPN C0805C223F3GECAUTO
C4, C5, C7, C10, C11: 0.1uF; C_0603_1608Metric; MPN C0603C103F3GECAUTO
C6: 1000uF; CAP_PC_10X12P7_NCH; MPN PCG1A102MCL1GS
C8: 10uF; R_1206_3216Metric; MPN F951E106KAAAQ2
C14: 300pF; C_0805_2012Metric; MPN 08053C301JAT2A
C16: 33pF; R_0402_1005Metric; MPN GJM1555C1H330FB01D
D1, D2, D3: D_Schottky; VS_30BQ015_M3_9AT; MPN VS-30BQ015-M3/9AT
F1, F2, F3: Fuse; FUSE_4628; MPN 36-4628-ND
H1, H2, H3, H4: MountingHole; MountingHole_3.2mm_M3; MPN NA
J1: Barrel_Jack; BarrelJack_CUI_PJ-102AH_Horizontal; MPN PJ-102AH
J2: 12V IN; Molex_KK-254_AE-6410-02A_1x02_P2.54mm_Vertical; MPN 1718560102
J3: 3v3 Backup; Molex_KK-254_AE-6410-02A_1x02_P2.54mm_Vertical; MPN 1718560102
J4: 3v3; Molex_KK-254_AE-6410-02A_1x02_P2.54mm_Vertical; MPN 1718560102
J5: 5V OUT; Molex_KK-254_AE-6410-02A_1x02_P2.54mm_Vertical; MPN 1718560102
JP1, JP2, JP3: SolderJumper_2_Open; SolderJumper-2_P1.3mm_Open_RoundedPad1.0x1.5mm; MPN NA
L1: 4.2uH; WE-TPC_5828; MPN 744053004
L2: 6.8uH; WE-PD_6050R; MPN 7447786006
R1: 191k; R_1210_3225Metric; MPN ERJ-14NF1913U
R2: 49.9k; R_2512_6332Metric; MPN RMCF2512FT49K9
R3: 499k; R_0805_2012Metric; MPN RCS0805499KFKEA
R4: 100k; R_0805_2012Metric; MPN RC0805FR-07100KL
R5: 7.5k; R_0805_2012Metric; MPN CRCW08057K50FKEAHP
R6, R7, R12: 10k; R_1206_3216Metric; MPN HRG3216P-1002-B-T1
R8: 10; R_2512_6332Metric; MPN CRGP2512F10R
R9: 33k; R_0805_2012Metric; MPN RCS080533K0FKEA
R10: 12.7k; R_1210_3225Metric; MPN CRCW121012K7FKEA
R11: 90.9k; R_1206_3216Metric; MPN RNCP1206FTD90K9
R13: 40.2k; R_0805_2012Metric; MPN CRCW080540K2FKEAHP
R14: 100k; R_0805_2012Metric; MPN RC0805FR-07100KL; not fitted
TP1: 12V; TestPoint_Keystone_5010-5014_Multipurpose; MPN 36-5010-ND
TP2: GND; TestPoint_Keystone_5010-5014_Multipurpose; MPN 36-5011-ND
U1: MP2338GTL-Z; SOT583_MP2338_MNP; MPN MP2338GTL-Z
U2: MP2315SGJ-Z; TSOT23-8_MP2315S_MNP; MPN MP2315SGJ-Z
U3: AMS1117-3.3; SOT-223-3_TabPin2; MPN AMS1117-3.3

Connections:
+5V: D3.2 (A), J1.1
+12V: D1.2 (A), D2.2 (A), J2.2, TP1.1
/VIN: C1.1, C4.1, F1.1, R1.1, U1.2 (VIN)
unnamed: C11.1, R8.2
unnamed: C14.2, R7.2, R11.2, R12.1
unnamed: C16.1, R9.2, R10.1, R13.2
unnamed: D1.1 (K), F1.2
unnamed: D2.1 (K), F2.2
unnamed: D3.1 (K), F3.2
unnamed: J3.1, JP1.2 (B)
unnamed: J4.1, JP2.2 (B)
unnamed: J5.1, JP3.2 (B)
unnamed: C9.1, JP1.1 (A), U3.2 (VO)
unnamed: C15.1, C16.2, C17.1, JP2.1 (A), L1.2, R13.1
unnamed: C12.1, C13.1, C14.1, JP3.1 (A), L2.2, R6.2, R11.1, R14.1
unnamed: C10.1, U1.5 (BST)
unnamed: R1.2, R2.1, U1.6 (EN)
unnamed: R7.1, U1.8 (FB)
unnamed: R6.1, U1.1 (PG)
unnamed: C3.2, U1.7 (SS)
unnamed: C10.2, L2.1, U1.3 (SW)
unnamed: C7.1, R4.2, R5.1, U2.1 (AAM)
unnamed: R8.1, U2.5 (BST)
unnamed: R3.2, U2.6 (EN)
unnamed: R9.1, U2.8 (FB)
unnamed: C2.1, C5.1, F2.1, R3.1, U2.2 (IN)
unnamed: C11.2, L1.1, U2.3 (SW)
unnamed: R4.1, U2.7 (VCC)
unnamed: C6.1, C8.1, F3.1, U3.3 (VI)

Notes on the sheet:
5V Power Supply
3v3 Backup Power Supply
3v3 Power Supply

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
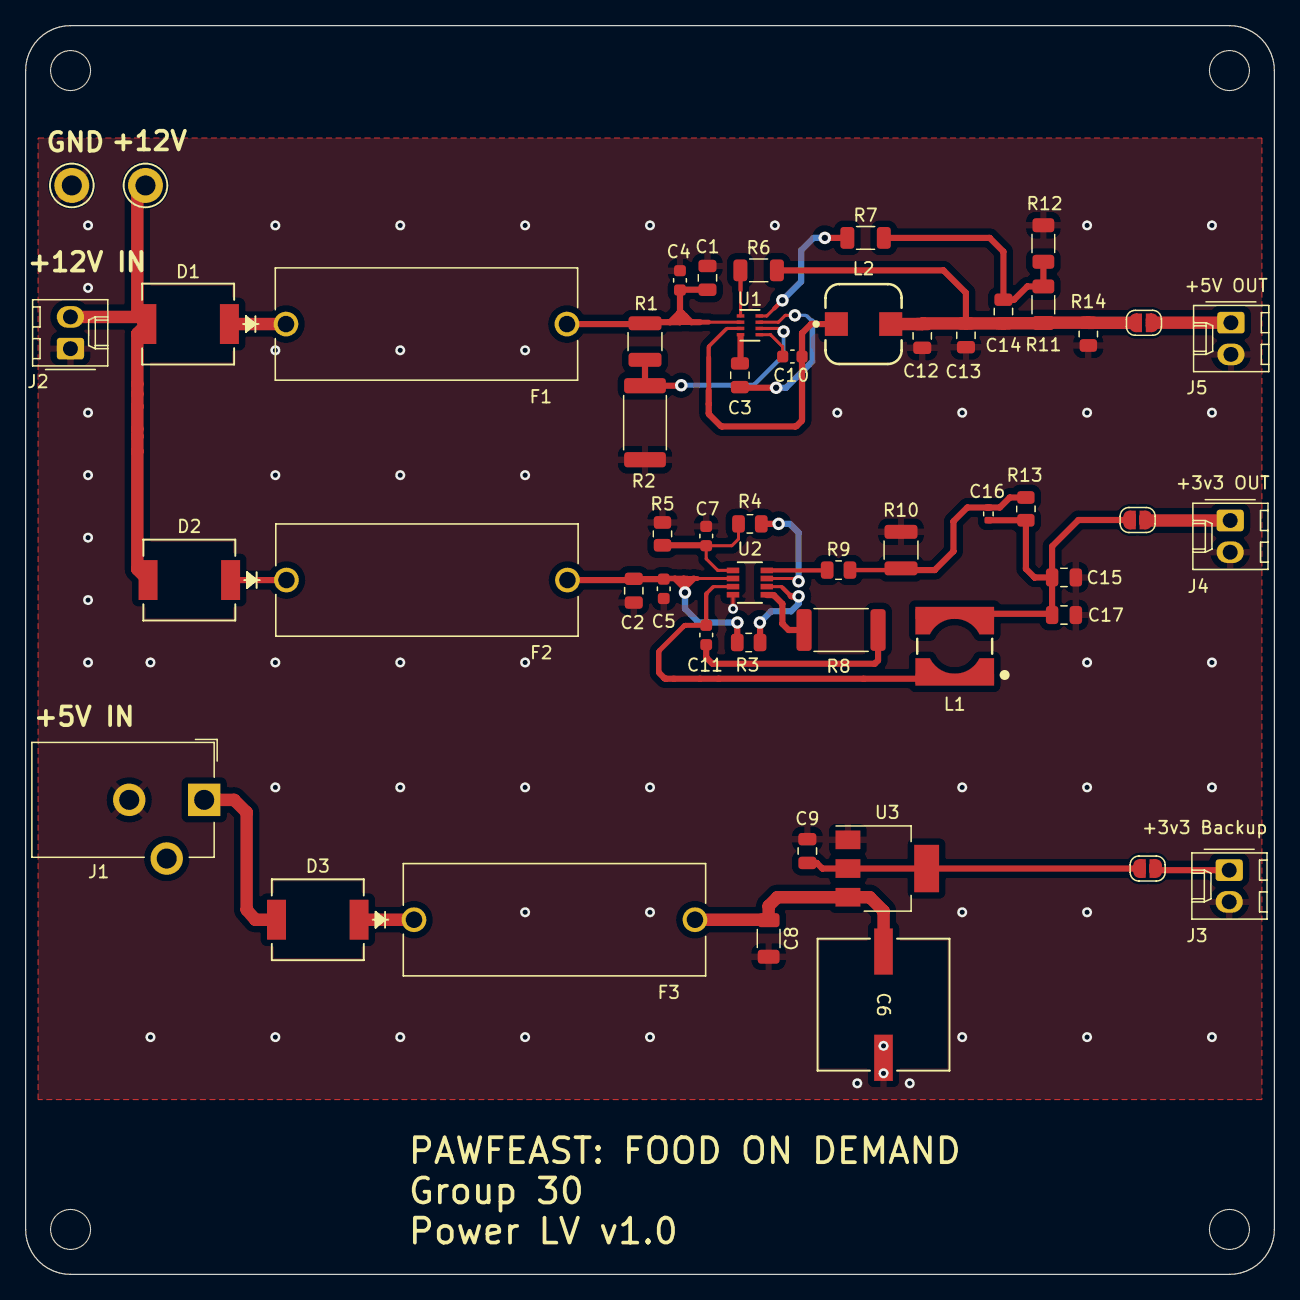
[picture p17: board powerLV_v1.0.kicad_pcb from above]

Board: 2 copper layers, 100.0 x 100.0 mm, 56 parts (0 on the bottom side), 31 nets.

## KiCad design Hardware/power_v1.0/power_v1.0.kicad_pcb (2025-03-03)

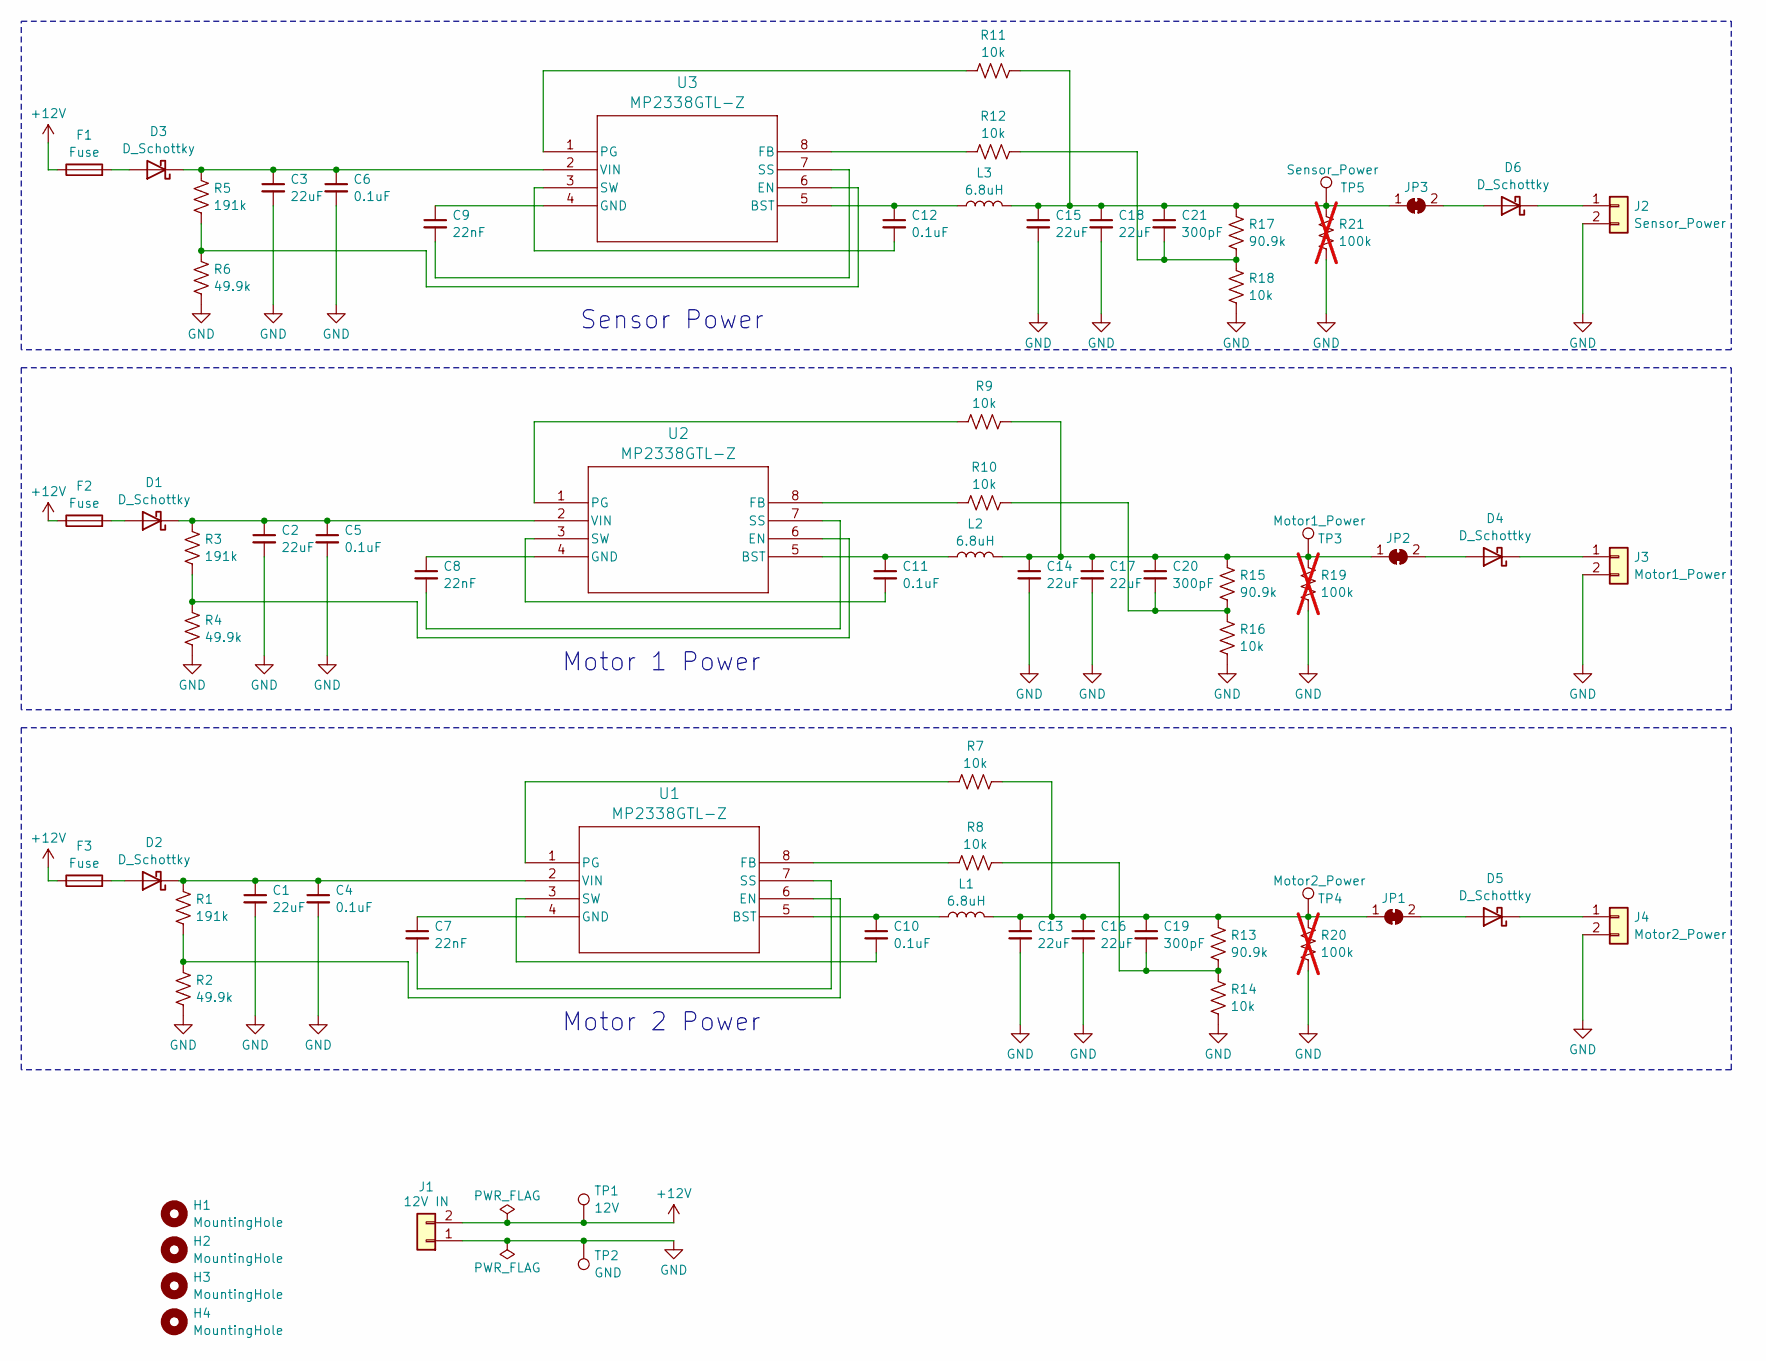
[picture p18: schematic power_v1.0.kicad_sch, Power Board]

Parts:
C1, C2, C3, C13, C14, C15, C16, C17, C18: 22uF; C_0805_2012Metric; MPN CL21A226MAYNNNE
C4, C5, C6, C10, C11, C12: 0.1uF; C_0603_1608Metric; MPN C0603C103F3GECAUTO
C7, C8, C9: 22nF; C_0805_2012Metric; MPN C0805C223F3GECAUTO
C19, C20, C21: 300pF; C_0805_2012Metric; MPN 08053C301JAT2A
D1, D2, D3, D4, D5, D6: D_Schottky; VS_30BQ015_M3_9AT; MPN VS-30BQ015-M3/9AT
F1, F2, F3: Fuse; FUSE_4628; MPN 36-4628-ND
H1, H2, H3, H4: MountingHole; MountingHole_3.2mm_M3; MPN NA
J1: 12V IN; Molex_KK-254_AE-6410-02A_1x02_P2.54mm_Vertical; MPN 1718560102
J2: Sensor_Power; Molex_KK-254_AE-6410-02A_1x02_P2.54mm_Vertical; MPN 1718560102
J3: Motor1_Power; Molex_KK-254_AE-6410-02A_1x02_P2.54mm_Vertical; MPN 1718560102
J4: Motor2_Power; Molex_KK-254_AE-6410-02A_1x02_P2.54mm_Vertical; MPN 1718560102
JP1, JP2, JP3: SolderJumper_2_Bridged; SolderJumper-2_P1.3mm_Bridged_RoundedPad1.0x1.5mm; MPN NA
L1, L2, L3: 6.8uH; WE-PD_6050R; MPN 7447786006
R1, R3, R5: 191k; R_1210_3225Metric; MPN ERJ-14NF1913U
R2, R4, R6: 49.9k; R_2512_6332Metric; MPN RMCF2512FT49K9
R7, R8, R9, R10, R11, R12, R14, R16, R18: 10k; R_1206_3216Metric; MPN HRG3216P-1002-B-T1
R13, R15, R17: 90.9k; R_1206_3216Metric; MPN RNCP1206FTD90K9
R19, R20, R21: 100k; R_0805_2012Metric; MPN RC0805FR-07100KL; not fitted
TP1: 12V; TestPoint_Keystone_5010-5014_Multipurpose; MPN 36-5010-ND
TP2: GND; TestPoint_Keystone_5010-5014_Multipurpose; MPN 36-5011-ND
TP3: Motor1_Power; TestPoint_Keystone_5010-5014_Multipurpose; MPN 36-5011-ND
TP4: Motor2_Power; TestPoint_Keystone_5010-5014_Multipurpose; MPN 36-5011-ND
TP5: Sensor_Power; TestPoint_Keystone_5010-5014_Multipurpose; MPN 36-5011-ND
U1, U2, U3: MP2338GTL-Z; SOT583_MP2338_MNP; MPN MP2338GTL-Z

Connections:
+12V: F1.1, F2.1, F3.1, J1.2, TP1.1
GND: C1.2, C2.2, C3.2, C4.2, C5.2, C6.2, C13.2, C14.2, C15.2, C16.2, C17.2, C18.2, J1.1, J2.2, J3.2, J4.2, R2.2, R4.2, R6.2, R14.2, R16.2, R18.2, R19.2, R20.2, R21.2, TP2.1
unnamed: C19.2, R8.2, R13.2, R14.1
unnamed: C20.2, R10.2, R15.2, R16.1
unnamed: C21.2, R12.2, R17.2, R18.1
unnamed: D1.2 (A), F2.2
unnamed: C2.1, C5.1, D1.1 (K), R3.1, U2.2 (VIN)
unnamed: D2.2 (A), F3.2
unnamed: C1.1, C4.1, D2.1 (K), R1.1, U1.2 (VIN)
unnamed: D3.2 (A), F1.2
unnamed: C3.1, C6.1, D3.1 (K), R5.1, U3.2 (VIN)
unnamed: D4.2 (A), JP2.2 (B)
unnamed: D4.1 (K), J3.1
unnamed: D5.2 (A), JP1.2 (B)
unnamed: D5.1 (K), J4.1
unnamed: D6.2 (A), JP3.2 (B)
unnamed: D6.1 (K), J2.1
unnamed: C13.1, C16.1, C19.1, JP1.1 (A), L1.2, R7.2, R13.1, R20.1, TP4.1
unnamed: C14.1, C17.1, C20.1, JP2.1 (A), L2.2, R9.2, R15.1, R19.1, TP3.1
unnamed: C15.1, C18.1, C21.1, JP3.1 (A), L3.2, R11.2, R17.1, R21.1, TP5.1
unnamed: C10.1, L1.1, U1.5 (BST)
unnamed: R1.2, R2.1, U1.6 (EN)
unnamed: R8.1, U1.8 (FB)
unnamed: C7.1, U1.4 (GND)
unnamed: R7.1, U1.1 (PG)
unnamed: C7.2, U1.7 (SS)
unnamed: C10.2, U1.3 (SW)
unnamed: C11.1, L2.1, U2.5 (BST)
unnamed: R3.2, R4.1, U2.6 (EN)
unnamed: R10.1, U2.8 (FB)
unnamed: C8.1, U2.4 (GND)
unnamed: R9.1, U2.1 (PG)
unnamed: C8.2, U2.7 (SS)
unnamed: C11.2, U2.3 (SW)
unnamed: C12.1, L3.1, U3.5 (BST)
unnamed: R5.2, R6.1, U3.6 (EN)
unnamed: R12.1, U3.8 (FB)
unnamed: C9.1, U3.4 (GND)
unnamed: R11.1, U3.1 (PG)
unnamed: C9.2, U3.7 (SS)
unnamed: C12.2, U3.3 (SW)

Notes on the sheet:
Motor 2 Power
Motor 1 Power
Sensor Power

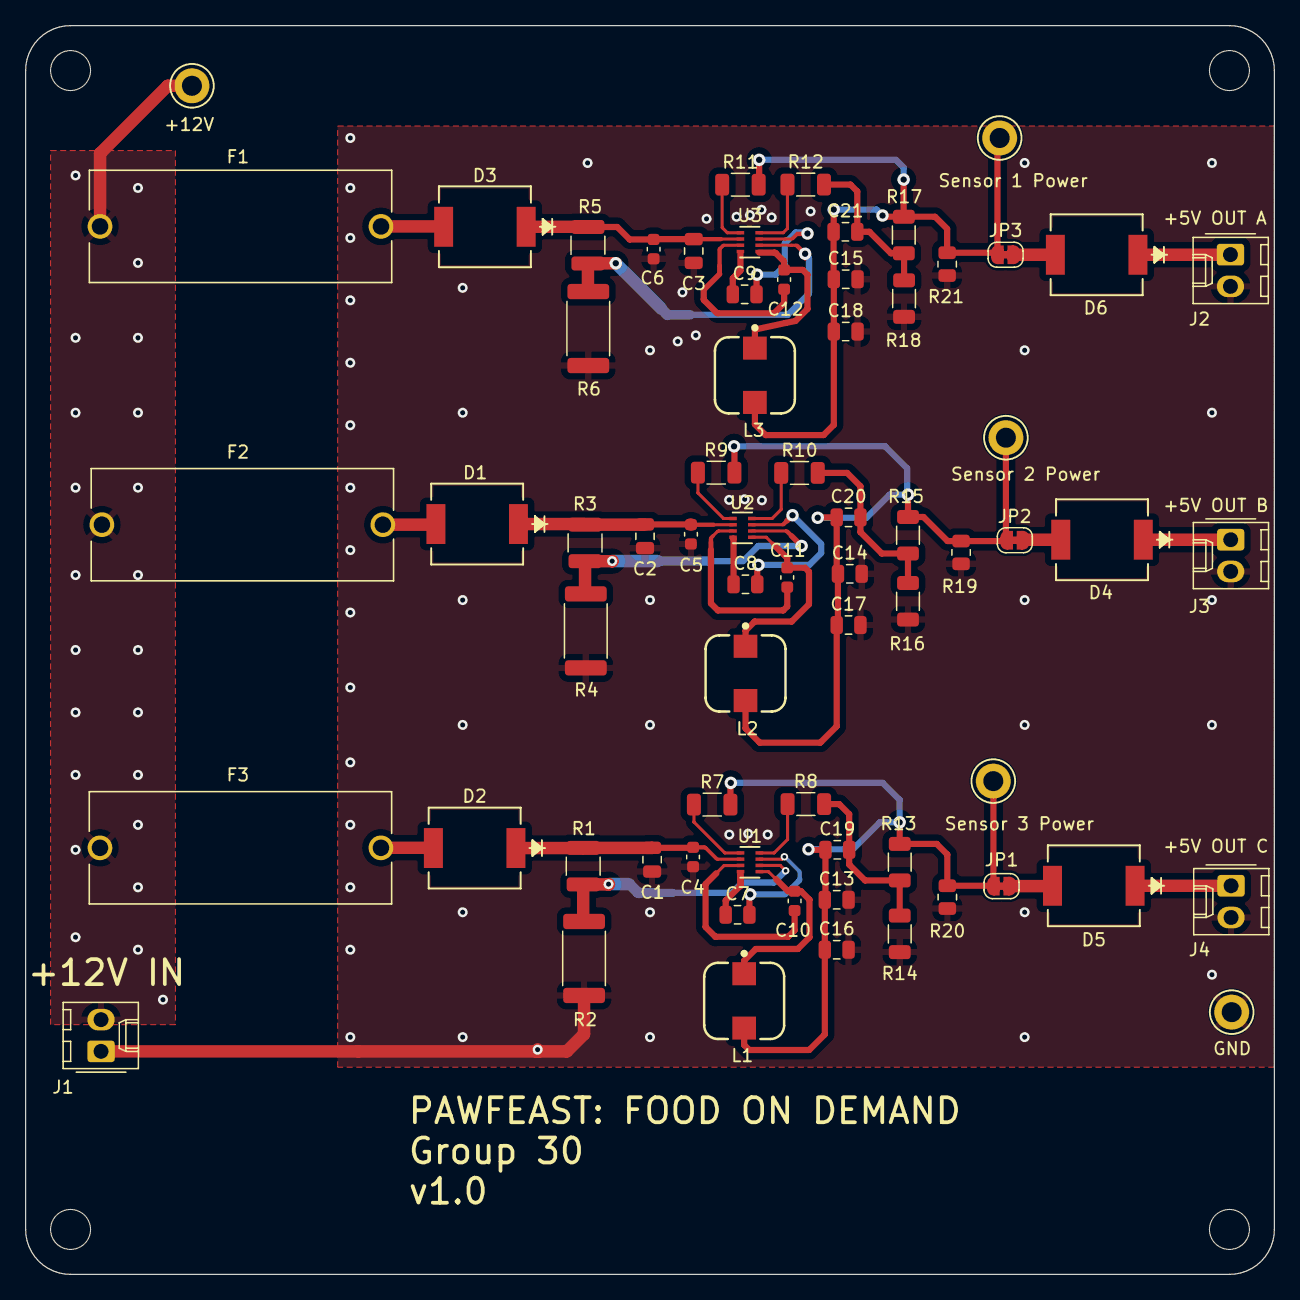
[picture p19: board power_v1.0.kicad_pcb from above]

Board: 2 copper layers, 100.0 x 100.0 mm, 73 parts (0 on the bottom side), 41 nets.

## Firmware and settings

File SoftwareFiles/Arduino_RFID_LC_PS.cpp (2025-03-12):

//Libraries
#include <SPI.h>		//RFID 
#include <MFRC522.h>
#include <Adafruit_NAU7802.h>	//LC

//Arduino Pin Definitions
#define RST_PIN   9       	//RFID
#define SS_PIN    10  
#define SENSORPIN 4		//PS

//RFID Definition
MFRC522 mfrc522(SS_PIN, RST_PIN);   // Create MFRC522 instance.
MFRC522::MIFARE_Key key;

//PS state definition
int sensorState = 0, lastState=0;         // variable for reading the pushbutton status

//LC definition
Adafruit_NAU7802 nau;


void setup() {
    Serial.begin(9600); // Initialize serial communications with the PC
    
    //**************************************
		//Start code for RFID
    while (!Serial);    // Do nothing if no serial port is opened (added for Arduinos based on ATMEGA32U4)
    SPI.begin();        // Init SPI bus
    mfrc522.PCD_Init(); // Init MFRC522 card

    // Prepare the key (used both as key A and as key B)
    // using FFFFFFFFFFFFh which is the default at chip delivery from the factory
    for (byte i = 0; i < 6; i++) {
        key.keyByte[i] = 0xFF;
    }

    Serial.println(F("Scan a MIFARE Classic PICC to demonstrate read and write."));
    Serial.print(F("Using key (for A and B):"));
    dump_byte_array(key.keyByte, MFRC522::MF_KEY_SIZE);
    Serial.println();

    Serial.println(F("BEWARE: Data will be written to the PICC, in sector #1"));
    
    
    //**************************************
    //Start setup for the infrared presence sensor
    // initialize the LED pin as an output:
	  pinMode(LED_BUILTIN, OUTPUT);      
	  // initialize the sensor pin as an input:
	  pinMode(SENSORPIN, INPUT);     
	  //digitalWrite(SENSORPIN, HIGH); // turn on the pullup //comment this out
	  
	  
	  //**************************************
		//Start code for load cell
	  Serial.print("NAU7802");
	  if (! nau.begin()) {
	    Serial.print("Failed to find NAU7802");
	    while (1) delay(10);  // Don't proceed.
	  }
	  Serial.print("Found NAU7802");
	
	  nau.setLDO(NAU7802_3V0);
	  Serial.print("LDO voltage set to ");
	  switch (nau.getLDO()) {
	    case NAU7802_4V5:  Serial.println("4.5V"); break;
	    case NAU7802_4V2:  Serial.println("4.2V"); break;
	    case NAU7802_3V9:  Serial.println("3.9V"); break;
	    case NAU7802_3V6:  Serial.println("3.6V"); break;
	    case NAU7802_3V3:  Serial.println("3.3V"); break;
	    case NAU7802_3V0:  Serial.println("3.0V"); break;
	    case NAU7802_2V7:  Serial.println("2.7V"); break;
	    case NAU7802_2V4:  Serial.println("2.4V"); break;
	    case NAU7802_EXTERNAL:  Serial.println("External"); break;
	  }
	
	  nau.setGain(NAU7802_GAIN_128);
	  Serial.print("Gain set to ");
	  switch (nau.getGain()) {
	    case NAU7802_GAIN_1:  Serial.println("1x"); break;
	    case NAU7802_GAIN_2:  Serial.println("2x"); break;
	    case NAU7802_GAIN_4:  Serial.println("4x"); break;
	    case NAU7802_GAIN_8:  Serial.println("8x"); break;
	    case NAU7802_GAIN_16:  Serial.println("16x"); break;
	    case NAU7802_GAIN_32:  Serial.println("32x"); break;
	    case NAU7802_GAIN_64:  Serial.println("64x"); break;
	    case NAU7802_GAIN_128:  Serial.println("128x"); break;
	  }
	
	  nau.setRate(NAU7802_RATE_10SPS);
	  Serial.print("Conversion rate set to ");
	  switch (nau.getRate()) {
	    case NAU7802_RATE_10SPS:  Serial.println("10 SPS"); break;
	    case NAU7802_RATE_20SPS:  Serial.println("20 SPS"); break;
	    case NAU7802_RATE_40SPS:  Serial.println("40 SPS"); break;
	    case NAU7802_RATE_80SPS:  Serial.println("80 SPS"); break;
	    case NAU7802_RATE_320SPS:  Serial.println("320 SPS"); break;
	  }
	
	  // Take 10 readings to flush out readings
	  for (uint8_t i=0; i<10; i++) {
	    while (! nau.available()) delay(1);
	    nau.read();
	  }
	
	  while (! nau.calibrate(NAU7802_CALMOD_INTERNAL)) {
	    Serial.println("Failed to calibrate internal offset, retrying!");
	    delay(1000);
	  }
	  Serial.println("Calibrated internal offset");
	
	  while (! nau.calibrate(NAU7802_CALMOD_OFFSET)) {
	    Serial.println("Failed to calibrate system offset, retrying!");
	    delay(1000);
	  }
	  Serial.println("Calibrated system offset");
}


void loop() {
		//**************************************
		//Start of infrared Presence sensor
    sensorState = digitalRead(SENSORPIN);
        
	  // check if the sensor beam is broken
	  // if it is, the sensorState is LOW:
	  if (sensorState == LOW) {     
	    // turn LED on:
	    digitalWrite(LED_BUILTIN, HIGH);  
	  } 
	  else {
	    // turn LED off:
	    digitalWrite(LED_BUILTIN, LOW); 
	  }
	  
	  if (sensorState) {           //print continuously
	    Serial.println("Unbroken");
	  } 
	  if (!sensorState) {
	    Serial.println("Broken");
	  }
		
		//**************************************
		//Start code for load cell
	  while (! nau.available()) {
	    delay(1);
	  }
	  int32_t val = nau.read();
	  Serial.print("Read "); Serial.println(val);
		

		//**************************************
		delay(2000);         // delay to not spam terminal and be able to see what we are doing
		
		//**************************************
		// start of RFID
    // Reset the loop if no new card present on the sensor/reader. This saves the entire process when idle.
    if ( ! mfrc522.PICC_IsNewCardPresent())
        return;

    // Select one of the cards
    if ( ! mfrc522.PICC_ReadCardSerial())
        return;

    // Show some details of the PICC (that is: the tag/card)
    Serial.print(F("Card UID:"));
    dump_byte_array(mfrc522.uid.uidByte, mfrc522.uid.size);
    Serial.println();
    Serial.print(F("PICC type: "));
    MFRC522::PICC_Type piccType = mfrc522.PICC_GetType(mfrc522.uid.sak);
    Serial.println(mfrc522.PICC_GetTypeName(piccType));

    // Check for compatibility
    if (    piccType != MFRC522::PICC_TYPE_MIFARE_MINI
        &&  piccType != MFRC522::PICC_TYPE_MIFARE_1K
        &&  piccType != MFRC522::PICC_TYPE_MIFARE_4K) {
        Serial.println(F("This sample only works with MIFARE Classic cards."));
        return;
    }

    // In this sample we use the second sector,
    // that is: sector #1, covering block #4 up to and including block #7
    byte sector         = 1;
    byte blockAddr      = 4;
    byte dataBlock[]    = {
        0x01, 0x02, 0x03, 0x04, //  1,  2,   3,  4,
        0x05, 0x06, 0x07, 0x08, //  5,  6,   7,  8,
        0x09, 0x0a, 0xff, 0x0b, //  9, 10, 255, 11,
        0x0c, 0x0d, 0x0e, 0x0f  // 12, 13, 14, 15
    };
    byte trailerBlock   = 7;
    MFRC522::StatusCode status;
    byte buffer[18];
    byte size = sizeof(buffer);

    // Authenticate using key A
    Serial.println(F("Authenticating using key A..."));
    status = (MFRC522::StatusCode) mfrc522.PCD_Authenticate(MFRC522::PICC_CMD_MF_AUTH_KEY_A, trailerBlock, &key, &(mfrc522.uid));
    if (status != MFRC522::STATUS_OK) {
        Serial.print(F("PCD_Authenticate() failed: "));
        Serial.println(mfrc522.GetStatusCodeName(status));
        return;
    }

    // Show the whole sector as it currently is
    Serial.println(F("Current data in sector:"));
    mfrc522.PICC_DumpMifareClassicSectorToSerial(&(mfrc522.uid), &key, sector);
    Serial.println();

    // Read data from the block
    Serial.print(F("Reading data from block ")); Serial.print(blockAddr);
    Serial.println(F(" ..."));
    status = (MFRC522::StatusCode) mfrc522.MIFARE_Read(blockAddr, buffer, &size);
    if (status != MFRC522::STATUS_OK) {
        Serial.print(F("MIFARE_Read() failed: "));
        Serial.println(mfrc522.GetStatusCodeName(status));
    }
    Serial.print(F("Data in block ")); Serial.print(blockAddr); Serial.println(F(":"));
    dump_byte_array(buffer, 16); Serial.println();
    Serial.println();

    // Authenticate using key B
    Serial.println(F("Authenticating again using key B..."));
    status = (MFRC522::StatusCode) mfrc522.PCD_Authenticate(MFRC522::PICC_CMD_MF_AUTH_KEY_B, trailerBlock, &key, &(mfrc522.uid));
    if (status != MFRC522::STATUS_OK) {
        Serial.print(F("PCD_Authenticate() failed: "));
        Serial.println(mfrc522.GetStatusCodeName(status));
        return;
    }

    // Write data to the block
    Serial.print(F("Writing data into block ")); Serial.print(blockAddr);
    Serial.println(F(" ..."));
    dump_byte_array(dataBlock, 16); Serial.println();
    status = (MFRC522::StatusCode) mfrc522.MIFARE_Write(blockAddr, dataBlock, 16);
    if (status != MFRC522::STATUS_OK) {
        Serial.print(F("MIFARE_Write() failed: "));
        Serial.println(mfrc522.GetStatusCodeName(status));
    }
    Serial.println();

    // Read data from the block (again, should now be what we have written)
    Serial.print(F("Reading data from block ")); Serial.print(blockAddr);
    Serial.println(F(" ..."));
    status = (MFRC522::StatusCode) mfrc522.MIFARE_Read(blockAddr, buffer, &size);
    if (status != MFRC522::STATUS_OK) {
        Serial.print(F("MIFARE_Read() failed: "));
        Serial.println(mfrc522.GetStatusCodeName(status));
    }
    Serial.print(F("Data in block ")); Serial.print(blockAddr); Serial.println(F(":"));
    dump_byte_array(buffer, 16); Serial.println();

    // Check that data in block is what we have written
    // by counting the number of bytes that are equal
    Serial.println(F("Checking result..."));
    byte count = 0;
    for (byte i = 0; i < 16; i++) {
        // Compare buffer (= what we've read) with dataBlock (= what we've written)
        if (buffer[i] == dataBlock[i])
            count++;
    }
    Serial.print(F("Number of bytes that match = ")); Serial.println(count);
    if (count == 16) {
        Serial.println(F("Success :-)"));
    } else {
        Serial.println(F("Failure, no match :-("));
        Serial.println(F("  perhaps the write didn't work properly..."));
    }
    Serial.println();

    // Dump the sector data
    Serial.println(F("Current data in sector:"));
    mfrc522.PICC_DumpMifareClassicSectorToSerial(&(mfrc522.uid), &key, sector);
    Serial.println();

    // Halt PICC
    mfrc522.PICC_HaltA();
    // Stop encryption on PCD
    mfrc522.PCD_StopCrypto1();
    
}

/**
 * Helper routine to dump a byte array as hex values to Serial.
 */
void dump_byte_array(byte *buffer, byte bufferSize) {
    for (byte i = 0; i < bufferSize; i++) {
        Serial.print(buffer[i] < 0x10 ? " 0" : " ");
        Serial.print(buffer[i], HEX);
    }
}

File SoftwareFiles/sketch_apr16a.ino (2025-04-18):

#include <Wire.h>
#include <Adafruit_NAU7802.h>

Adafruit_NAU7802 nau;

#define VIN1_THRESHOLD 200000  // bowl press threshold
#define NAU7802_ADDR 0x2A
#define REG_CTRL2 0x02

void setup()
{
  Serial.begin(115200);
  delay(1000);
  Wire.begin(17, 16);   // SDA, SCL
  pinMode(21, INPUT);   // DRDY

  Serial.println("Initializing NAU7802...");
  if (!nau.begin())
  {
    Serial.println("Failed to find NAU7802");
    while (1) delay(10);
  }

  nau.setLDO(NAU7802_3V3);
  nau.setGain(NAU7802_GAIN_128);
  nau.setRate(NAU7802_RATE_10SPS);

  for (int i = 0; i < 10; i++)
  {
    while (!nau.available()) delay(1);
    nau.read();
  }

  while (!nau.calibrate(NAU7802_CALMOD_INTERNAL)) delay(1000);
  while (!nau.calibrate(NAU7802_CALMOD_OFFSET)) delay(1000);

  setChannel(false);  // Start with VIN1 (bowl)
}

void loop()
{
  // Always monitor VIN1 (bowl)
  setChannel(false);
  while (!nau.available()) delay(1);
  int32_t vin1_val = nau.read();

  Serial.print("VIN1 (bowl): ");
  Serial.println(vin1_val);

  if (vin1_val > VIN1_THRESHOLD)
  {
    Serial.println("Bowl pressed! Monitoring button for 10 seconds...");

    // Switch to VIN2 (button)
    setChannel(true);
    delay(50); // allow channel to settle

    unsigned long startTime = millis();
    int32_t last_button_val = 0;

    while (millis() - startTime < 10000)
    {
      while (!nau.available()) delay(1);
      int32_t vin2_val = nau.read();
      last_button_val = vin2_val;
      Serial.print("VIN2 (button): ");
      Serial.println(vin2_val);
      delay(200); // pace reads
    }

    Serial.print("Last VIN2 reading after 10 sec: ");
    Serial.println(last_button_val);

    // Switch back to VIN1
    setChannel(false);
    delay(500); // debounce or reset time
  }

  delay(100); // loop pacing
}

void setChannel(bool vin2)
{
  Wire.beginTransmission(NAU7802_ADDR);
  Wire.write(REG_CTRL2);
  Wire.endTransmission(false);
  Wire.requestFrom(NAU7802_ADDR, 1);
  if (Wire.available())
  {
    uint8_t ctrl2 = Wire.read();
    if (vin2)
      ctrl2 |= 0b10000000;
    else
      ctrl2 &= 0b01111111;

    Wire.beginTransmission(NAU7802_ADDR);
    Wire.write(REG_CTRL2);
    Wire.write(ctrl2);
    Wire.endTransmission();
  }
}

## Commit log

2025-01-23 Initial setup of KiCAD libraries and members digital notebooks
    [Template_v0.0.kicad_pcb, Template_v0.0.kicad_sch]
2025-02-25 created power and brain boards. Power has three regulators which output 5V for the motors/sensor, while brain will have the MCU, 3v3 regulator circuit, and level shifters among other things. Driver c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
    [Motor1_Power.kicad_sch, Motor2_Power.kicad_sch, Sensors_Power.kicad_sch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]
2025-02-26 almost finished design of power board and working through design of brain board
    [Motor1_Power.kicad_sch, Motor2_Power.kicad_sch, Power.kicad_sch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]
2025-02-27 brain design pretty much done if RFID not needed
    [Power.kicad_sch, brain_v1.0.kicad_sch]
2025-02-28 finished part selection for power and almost done with part selection for brain--moving to layout next
    [Motor1_Power.kicad_sch, Motor2_Power.kicad_sch, Power.kicad_sch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]
2025-02-28 everything done on design and parts for first board run except for ADC; onto layout
    [Power.kicad_sch, brain_v1.0.kicad_sch]
2025-03-01 finished part selection and schematic for brain. Created RFID and Motor Driver boards
    [MotorDriver_v1.0.kicad_pcb, MotorDriver_v1.0.kicad_sch, Power.kicad_sch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]
2025-03-02 brain fix and almost done with power board layout
    [Power.kicad_sch, power_v1.0.kicad_pcb, power_v1.0.kicad_sch]
2025-03-03 power board done
    [power_v1.0.kicad_pcb]
2025-03-07 RFID board schematic done, antenna head created in the layout
    [RFID_v1.0.kicad_sch, brain_v1.0.kicad_sch]
2025-03-09 RFID schematic done
    [RFID_v1.0.kicad_sch]
2025-03-10 made motor driver layout base and moved brain power to a separate board
    [brain_v1.0.kicad_sch, powerLV_v1.0.kicad_pcb, powerLV_v1.0.kicad_sch]
2025-03-10 instead of an onboard power, I decided to make a separate board for just brain power--essentially a second power board.
    [powerLV_v1.0.kicad_pcb, powerLV_v1.0.kicad_sch]
2025-03-10 started brain layout, can definitely be done in the 100x100 mm space
    [brain_v1.0.kicad_pcb, brain_v1.0.kicad_sch]
2025-03-11 Halfway done with the brain layout--had to fix some issues from the schematic and relink designators. I also added an md file in the Hardware library that specifies how someone can link the Solar Car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
    [4628.step, 6120XX21621_61200621621.step, NAU7802SGI.step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]
2025-03-12 more than halfway done with brain, optimizing routing
    [brain_v1.0.kicad_pcb, brain_v1.0.kicad_sch]
2025-03-13 working on brain layout
    [brain_v1.0.kicad_pcb]
2025-03-13 brain done! except for stitching vias
    [brain_v1.0.kicad_pcb, brain_v1.0.kicad_sch]
2025-03-13 done with brain v1
    [brain_v1.0.kicad_pcb]
2025-03-13 updated motor driver
    [MotorDriver_v1.0.kicad_pcb, MotorDriver_v1.0.kicad_sch]
2025-03-31 small change to powerLV
    [powerLV_v1.0.kicad_pcb]
2025-04-05 changed LV
    [powerLV_v1.0.kicad_pcb, powerLV_v1.0.kicad_sch]
2025-04-05 updated motor
    yes
    [MotorDriver_v1.0.kicad_pcb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]
2025-04-06 second version of brain
    [brain_v2.0.kicad_pcb, brain_v2.0.kicad_sch]
2025-04-15 Create ESP32_RFID_PS_LC.cpp
    This is the current integrated working code for the WIFI, RFID, PS, and LC. all routing is completed on the server end for the WIFI RFID and PS.
    - Need to differentiate the load cell readings and when they are pressed
    - Need to handle processing for server side of load cell to push a notification to history
2025-04-16 small fix to LV board
    [powerLV_v1.0.kicad_sch]
2025-04-17 added load cell files
    sketch16 differentiates on address
    test1_adc is adafruit code just wired to gpio
2025-04-18 creating PDS board and update other boards
    [PDS_v1.0.kicad_pcb, PDS_v1.0.kicad_sch, brain_v2.0.kicad_pcb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]
2025-04-19 PDS done
    [PDS_v1.0.kicad_pcb, PDS_v1.0.kicad_sch]
2025-04-19 gerbers for PDS
2025-04-19 fixed silkscreens + readability on PDS
    [PDS_v1.0.kicad_pcb, PDS_v1.0.kicad_sch]
